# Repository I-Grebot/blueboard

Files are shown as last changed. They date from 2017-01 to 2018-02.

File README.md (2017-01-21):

# BlueBoard v1

The BlueBoard is a small form-factor "all-in-one" electronic board for 2 wheels robots.

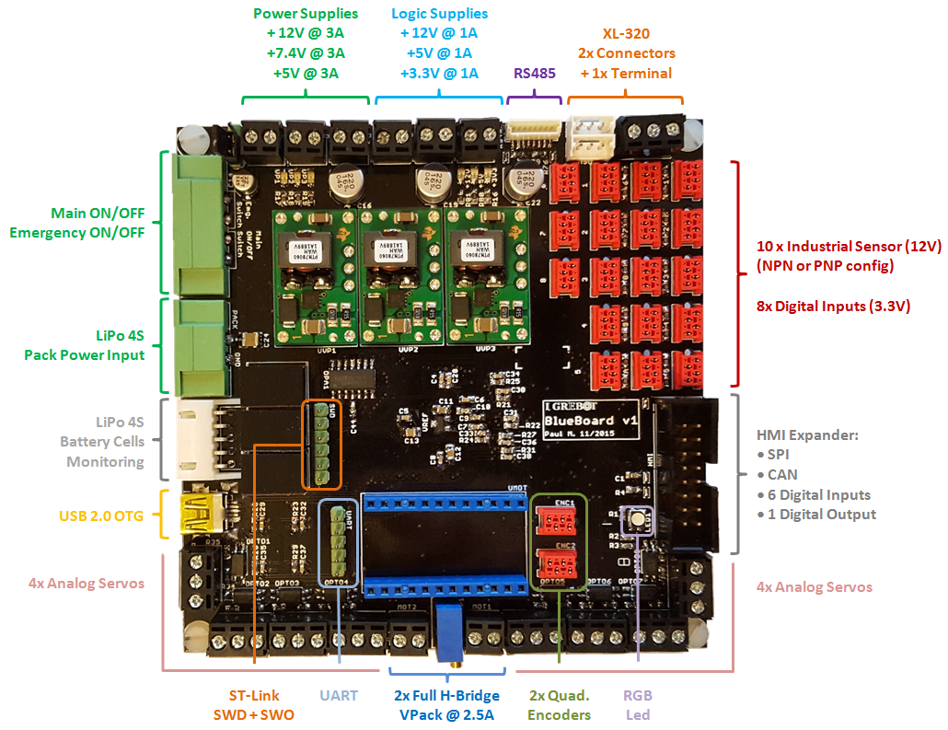
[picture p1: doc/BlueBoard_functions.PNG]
BlueBoard functions


## Features

The board features the following items:

* Compact size: 10 cm x 10 cm
* Single input power-supply (+14V min)
* Integrated Power-Supplies for logic domains using efficient DC/DC step-down regulators:
 * +12V/1A (industrial sensors)
 * +5V/1A (quadrature encoders, other 5V logic)
 * +3/3V/1A (most of digital logic)
* Integrated  Power-Supplies for heavy loads:
 * +12V/3A (generic purpose)
 * +7.4V/3A (dynamixel digital servos ~ can be adjusted)
 * +5V/3A (analog servos)
* Secure and robust Power-pack connector
* Main ON/OFF + Emergency switch connectors
* 2x Full H-Bridge output controls for DRV8842 (2.5A)
* 8x Opto-coupled analog-servos interface (PWM)
* 2x Connectors + 1x terminal for XL-320 digital servos interface
* 2x Quadrature encoders inputs
* 10x Opto-coupled Industrial sensor inputs (NPN/PNP  types selectable)
* 8x Digital Inputs
* RS485 connector for sensor-bus (to be used with ProxTof boards or other)
* UART with RTS/CTS signals
* USB 2.0 OTG connector
* ST-Link with SWD + SWO programming / debugging connector
* Expander connector (to be used with microBoard_HMI):
 * 1x SPI
 * 1x CAN
 * 6x Digital inputs (user selections switches)
 * 1x Digital outputs 

## Troubleshooting

* Mimimum input voltage (TEN / PTN modules) is high for 4S batteries (error due to 6S -> 4S design migration)
* Not working 4S battery cell monitoring analog circuit (to be further checked)

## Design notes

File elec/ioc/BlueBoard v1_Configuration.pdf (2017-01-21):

## BlueBoard Project Configuration Report

# 1. Description

## 1.1. Project

Project Name | BlueBoard
Board Name | BlueBoard
Generated with: | STM32CubeMX 4.12.0
Date | 01/02/2016

## 1.2. MCU

MCU Series | STM32F7
MCU Line | STM32F7x6
MCU name | STM32F746VGTx
MCU Package | LQFP100
MCU Pin number | 100

# 2. Pinout Configuration

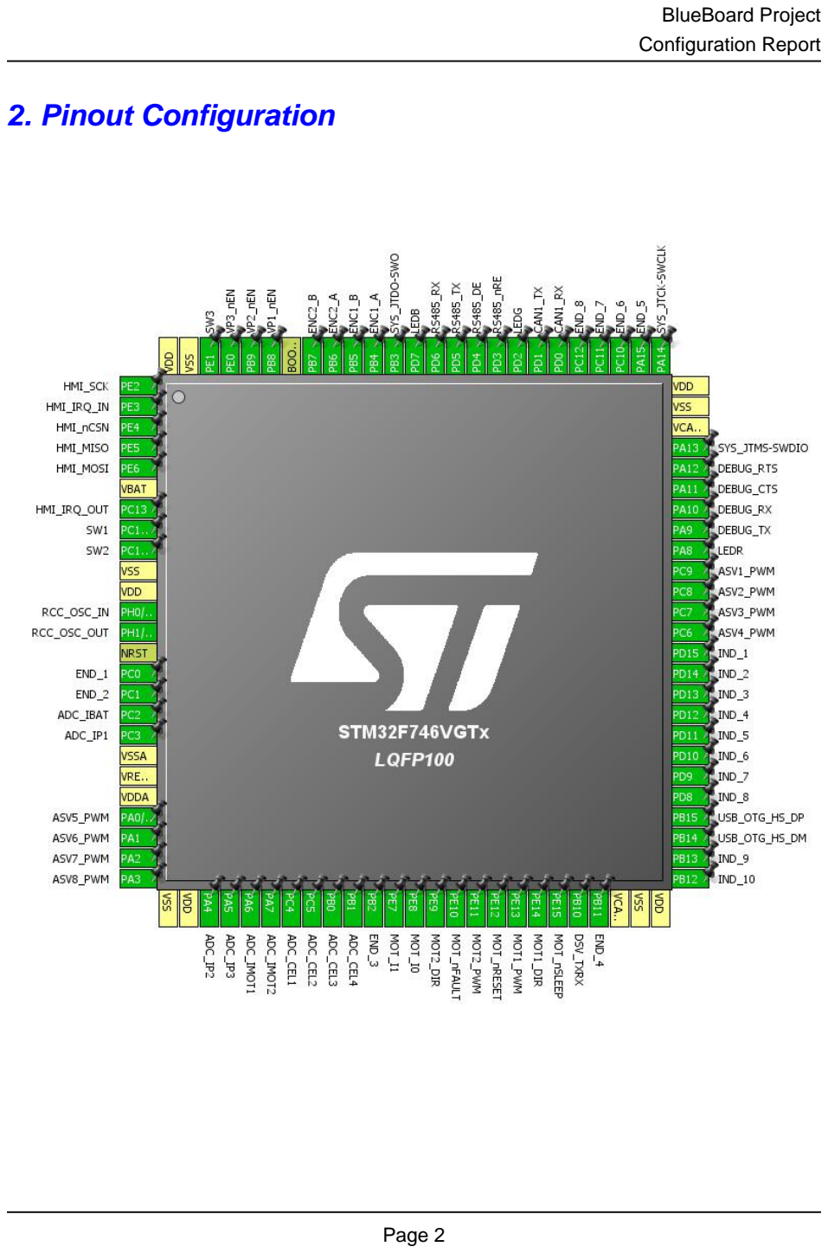
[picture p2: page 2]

# 3. Pins Configuration

Pin Number LQFP100 | Pin Name (function after reset) | Pin Type | Alternate Function(s) | Label
1 | PE2 | I/O | SPI4_SCK | HMI_SCK
2 | PE3 * | I/O | GPIO_Input | HMI_IRQ_IN
3 | PE4 | I/O | SPI4_NSS | HMI_nCSN
4 | PE5 | I/O | SPI4_MISO | HMI_MISO
5 | PE6 | I/O | SPI4_MOSI | HMI_MOSI
6 | VBAT | Power
7 | PC13 * | I/O | GPIO_Output | HMI_IRQ_OUT
8 | PC14/OSC32_IN * | I/O | GPIO_Input | SW1
9 | PC15/OSC32_OUT * | I/O | GPIO_Input | SW2
10 | VSS | Power
11 | VDD | Power
12 | PH0/OSC_IN | I/O | RCC_OSC_IN
13 | PH1/OSC_OUT | I/O | RCC_OSC_OUT
14 | NRST | Reset
15 | PC0 * | I/O | GPIO_Input | END_1
16 | PC1 * | I/O | GPIO_Input | END_2
17 | PC2 | I/O | ADC1_IN12 | ADC_IBAT
18 | PC3 | I/O | ADC1_IN13 | ADC_IP1
19 | VSSA | Power
20 | VREF+ | Power
21 | VDDA | Power
22 | PA0/WKUP | I/O | TIM5_CH1 | ASV5_PWM
23 | PA1 | I/O | TIM5_CH2 | ASV6_PWM
24 | PA2 | I/O | TIM5_CH3 | ASV7_PWM
25 | PA3 | I/O | TIM5_CH4 | ASV8_PWM
26 | VSS | Power
27 | VDD | Power
28 | PA4 | I/O | ADC1_IN4 | ADC_IP2
29 | PA5 | I/O | ADC1_IN5 | ADC_IP3
30 | PA6 | I/O | ADC1_IN6 | ADC_IMOT1
31 | PA7 | I/O | ADC1_IN7 | ADC_IMOT2
32 | PC4 | I/O | ADC1_IN14 | ADC_CEL1
33 | PC5 | I/O | ADC1_IN15 | ADC_CEL2
34 | PB0 | I/O | ADC1_IN8 | ADC_CEL3
35 | PB1 | I/O | ADC1_IN9 | ADC_CEL4
36 | PB2 * | I/O | GPIO_Input | END_3

Pin Number LQFP100 | Pin Name (function after reset) | Pin Type | Alternate Function(s) | Label
37 | PE7 * | I/O | GPIO_Output | MOT_I1
38 | PE8 * | I/O | GPIO_Output | MOT_I0
39 | PE9 | I/O | TIM1_CH1 | MOT2_DIR
40 | PE10 * | I/O | GPIO_Input | MOT_nFAULT
41 | PE11 | I/O | TIM1_CH2 | MOT2_PWM
42 | PE12 * | I/O | GPIO_Output | MOT_nRESET
43 | PE13 | I/O | TIM1_CH3 | MOT1_PWM
44 | PE14 | I/O | TIM1_CH4 | MOT1_DIR
45 | PE15 * | I/O | GPIO_Output | MOT_nSLEEP
46 | PB10 | I/O | USART3_TX | DSV_TXRX
47 | PB11 * | I/O | GPIO_Input | END_4
48 | VCAP_1 | Power
49 | VSS | Power
50 | VDD | Power
51 | PB12 * | I/O | GPIO_Input | IND_10
52 | PB13 * | I/O | GPIO_Input | IND_9
53 | PB14 | I/O | USB_OTG_HS_DM
54 | PB15 | I/O | USB_OTG_HS_DP
55 | PD8 * | I/O | GPIO_Input | IND_8
56 | PD9 * | I/O | GPIO_Input | IND_7
57 | PD10 * | I/O | GPIO_Input | IND_6
58 | PD11 * | I/O | GPIO_Input | IND_5
59 | PD12 * | I/O | GPIO_Input | IND_4
60 | PD13 * | I/O | GPIO_Input | IND_3
61 | PD14 * | I/O | GPIO_Input | IND_2
62 | PD15 * | I/O | GPIO_Input | IND_1
63 | PC6 | I/O | TIM8_CH1 | ASV4_PWM
64 | PC7 | I/O | TIM8_CH2 | ASV3_PWM
65 | PC8 | I/O | TIM8_CH3 | ASV2_PWM
66 | PC9 | I/O | TIM8_CH4 | ASV1_PWM
67 | PA8 * | I/O | GPIO_Output | LEDR
68 | PA9 | I/O | USART1_TX | DEBUG_TX
69 | PA10 | I/O | USART1_RX | DEBUG_RX
70 | PA11 | I/O | USART1_CTS | DEBUG_CTS
71 | PA12 | I/O | USART1_RTS | DEBUG_RTS
72 | PA13 | I/O | SYS_JTMS-SWDIO
73 | VCAP_2 | Power
74 | VSS | Power
75 | VDD | Power

Pin Number LQFP100 | Pin Name (function after reset) | Pin Type | Alternate Function(s) | Label
76 | PA14 | I/O | SYS_JTCK-SWCLK
77 | PA15 * | I/O | GPIO_Input | END_5
78 | PC10 * | I/O | GPIO_Input | END_6
79 | PC11 * | I/O | GPIO_Input | END_7
80 | PC12 * | I/O | GPIO_Input | END_8
81 | PD0 | I/O | CAN1_RX
82 | PD1 | I/O | CAN1_TX
83 | PD2 * | I/O | GPIO_Output | LEDG
84 | PD3 * | I/O | GPIO_Output | RS485_nRE
85 | PD4 * | I/O | GPIO_Output | RS485_DE
86 | PD5 | I/O | USART2_TX | RS485_TX
87 | PD6 | I/O | USART2_RX | RS485_RX
88 | PD7 * | I/O | GPIO_Output | LEDB
89 | PB3 | I/O | SYS_JTDO-SWO
90 | PB4 | I/O | TIM3_CH1 | ENC1_A
91 | PB5 | I/O | TIM3_CH2 | ENC1_B
92 | PB6 | I/O | TIM4_CH1 | ENC2_A
93 | PB7 | I/O | TIM4_CH2 | ENC2_B
94 | BOOT0 | Boot
95 | PB8 * | I/O | GPIO_Output | VP1_nEN
96 | PB9 * | I/O | GPIO_Output | VP2_nEN
97 | PE0 * | I/O | GPIO_Output | VP3_nEN
98 | PE1 * | I/O | GPIO_Input | SW3
99 | VSS | Power
100 | VDD | Power

## * The pin is affected with an I/O function

# 4. Clock Tree Configuration

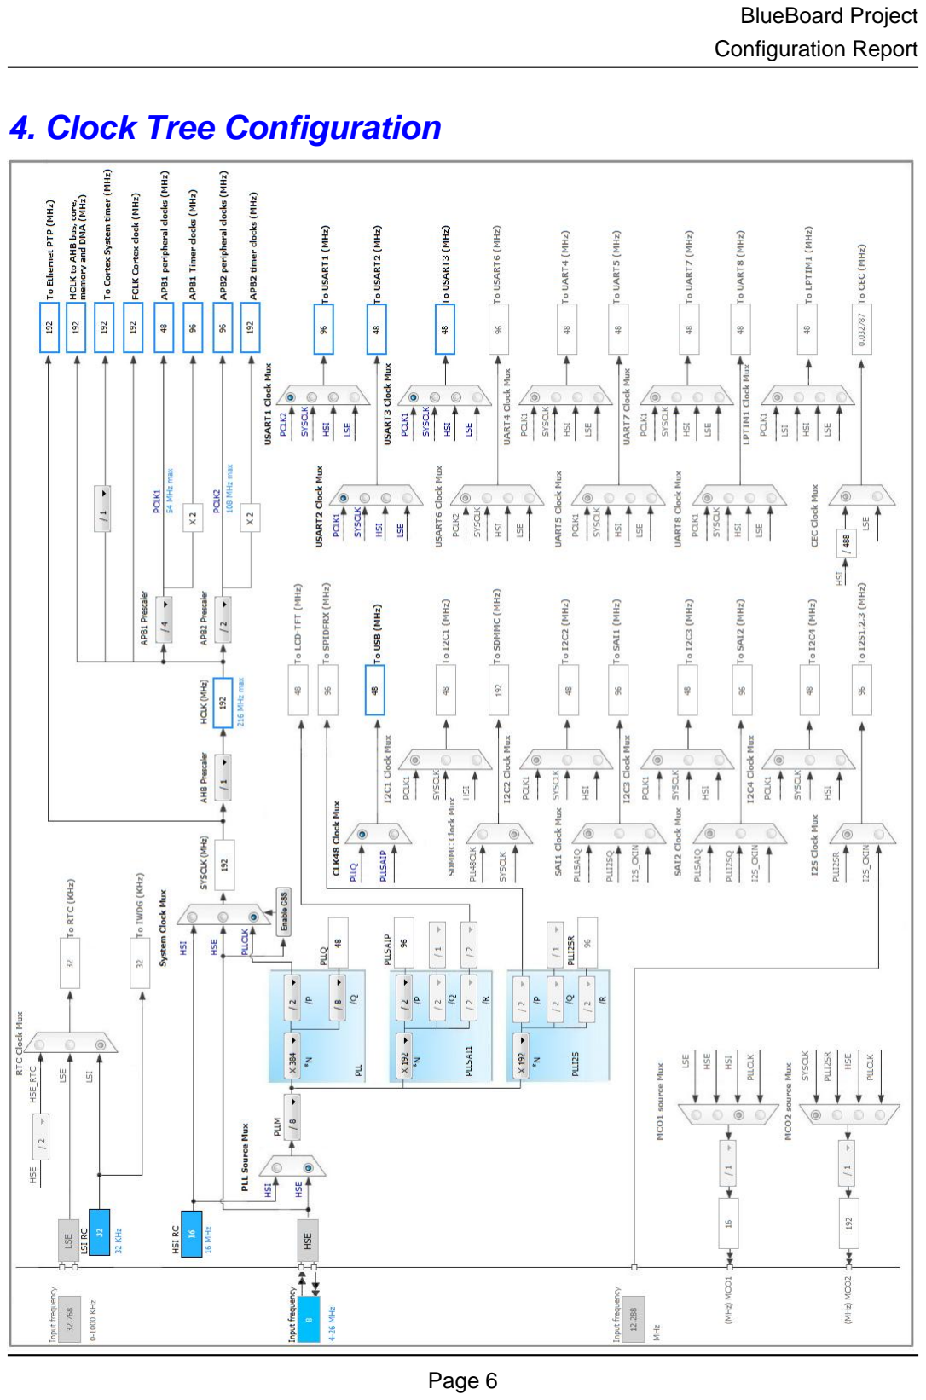
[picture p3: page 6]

# 5. IPs and Middleware Configuration

# 5.1. ADC1

## mode: IN4 mode: IN5 mode: IN6 mode: IN7 mode: IN8 mode: IN9 mode: IN12 mode: IN13 mode: IN14 mode: IN15

## 5.1.1. Parameter Settings:

### ADCs_Common_Settings:

Mode | Independent mode

### ADC_Settings:

Clock Prescaler | PCLK2 divided by 8 *
Resolution | 12 bits (15 ADC Clock cycles)
Data Alignment | Right alignment
Scan Conversion Mode | Disabled
Continuous Conversion Mode | Disabled
Discontinuous Conversion Mode | Disabled
DMA Continuous Requests | Disabled
End Of Conversion Selection | EOC flag at the end of all conversions *

### ADC_Regular_ConversionMode:

Number Of Conversion | 1
External Trigger Conversion Edge | None
Rank | 1
Channel | Channel 4
Sampling Time | 3 Cycles

### ADC_Injected_ConversionMode:

Number Of Conversions | 0

### WatchDog:

Enable Analog WatchDog Mode | false

# 5.2. CAN1

## mode: Mode

## 5.2.1. Parameter Settings:

### Bit Timings Parameters:

Prescaler (for Time Quantum) | 16
Time Quantum | 333.3333333333333 *
Time Quanta in Bit Segment 1 | 6 Times *
Time Quanta in Bit Segment 2 | 5 Times *
Time for one Bit | 4000 *
ReSynchronization Jump Width | 3 Times *

### Basic Parameters:

Time Triggered Communication Mode | Disable
Automatic Bus-Off Management | Disable
Automatic Wake-Up Mode | Disable
No-Automatic Retransmission | Disable
Receive Fifo Locked Mode | Disable
Transmit Fifo Priority | Disable

### Advanced Parameters:

Operating Mode | Normal

# 5.3. RCC

## High Speed Clock (HSE): Crystal/Ceramic Resonator

## 5.3.1. Parameter Settings:

### System Parameters:

VDD voltage (V) | 3.3
Flash Latency(WS) | 6 WS (7 CPU cycle)

### RCC Parameters:

HSI Calibration Value | 16
TIM Prescaler Selection | Disabled

### Power Parameters:

Power Over Drive | Enabled

Power Regulatror Voltage Scale | Power Regulator Voltage Scale 1

# 5.4. SPI4

## Mode: Full-Duplex Master mode: Hardware NSS Signal

## 5.4.1. Parameter Settings:

### Basic Parameters:

Frame Format | Motorola
Data Size | 16 Bits *
First Bit | MSB First

### Clock Parameters:

Prescaler (for Baud Rate) | 256 *
Baud Rate | 375.0 KBits/s *
Clock Polarity (CPOL) | Low
Clock Phase (CPHA) | 1 Edge

### Advanced Parameters:

CRC Calculation | Disabled
NSSP Mode | Enabled
NSS Signal Type | Output Hardware

# 5.5. SYS

## Debug: SWD and Asynchronous Trace

# 5.6. TIM1

## Channel1: PWM Generation CH1 Channel2: PWM Generation CH2 Channel3: PWM Generation CH3 Channel4: PWM Generation CH4

## 5.6.1. Parameter Settings:

### Counter Settings:

Prescaler (PSC - 16 bits value) | 0

Counter Mode | Up
Counter Period (AutoReload Register - 16 bits value ) | 0
Internal Clock Division (CKD) | No Division
Repetition Counter (RCR - 16 bits value) | 0

### Trigger Output (TRGO) Parameters:

Master/Slave Mode | Disable (no sync between this TIM (Master) and its Slaves
Trigger Event Selection TRGO | Reset (UG bit from TIMx_EGR)
Trigger Event Selection TRGO2 | Reset (UG bit from TIMx_EGR)

### Break And Dead Time management - BRK Configuration:

BRK State | Disable
BRK Polarity | High
BRK Filter (4 bits value) | 0

### Break And Dead Time management - BRK2 Configuration:

BRK2 State | Disable
BRK2 Polarity | High
BRK2 Filter (4 bits value) | 0

### Break And Dead Time management - Output Configuration:

Automatic Output State | Disable
Off State Selection for Run Mode (OSSR) | Disable
Off State Selection for Idle Mode (OSSI) | Disable
Lock Configuration | Off

### Clear Input:

Clear Input Source | Disable

### PWM Generation Channel 1:

Mode | PWM mode 1
Pulse (16 bits value) | 0
Fast Mode | Disable
CH Polarity | High
CH Idle State | Reset

### PWM Generation Channel 2:

Mode | PWM mode 1
Pulse (16 bits value) | 0
Fast Mode | Disable
CH Polarity | High
CH Idle State | Reset

### PWM Generation Channel 3:

Mode | PWM mode 1
Pulse (16 bits value) | 0
Fast Mode | Disable
CH Polarity | High
CH Idle State | Reset

### PWM Generation Channel 4:

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

# 5.7. TIM3

## Combined Channels: Encoder Mode

## 5.7.1. Parameter Settings:

### Counter Settings:

Prescaler (PSC - 16 bits value) | 0
Counter Mode | Up
Counter Period (AutoReload Register - 16 bits value ) | 0
Internal Clock Division (CKD) | No Division

### Trigger Output (TRGO) Parameters:

Master/Slave Mode | Disable (no sync between this TIM (Master) and its Slaves
Trigger Event Selection TRGO | Reset (UG bit from TIMx_EGR)

### Encoder:

Encoder Mode | Encoder Mode TI1
____ Parameters for Channel 1 ____
Polarity | Rising Edge
IC Selection | Direct
Prescaler Division Ratio | No division
Input Filter | 0
____ Parameters for Channel 2 ____
Polarity | Rising Edge
IC Selection | Direct
Prescaler Division Ratio | No division
Input Filter | 0

# 5.8. TIM4

## Combined Channels: Encoder Mode

## 5.8.1. Parameter Settings:

### Counter Settings:

Prescaler (PSC - 16 bits value) | 0
Counter Mode | Up
Counter Period (AutoReload Register - 16 bits value ) | 0
Internal Clock Division (CKD) | No Division

### Trigger Output (TRGO) Parameters:

Master/Slave Mode | Disable (no sync between this TIM (Master) and its Slaves
Trigger Event Selection TRGO | Reset (UG bit from TIMx_EGR)

### Encoder:

Encoder Mode | Encoder Mode TI1
____ Parameters for Channel 1 ____
Polarity | Rising Edge
IC Selection | Direct
Prescaler Division Ratio | No division
Input Filter | 0
____ Parameters for Channel 2 ____
Polarity | Rising Edge
IC Selection | Direct
Prescaler Division Ratio | No division
Input Filter | 0

# 5.9. TIM5

## Channel1: PWM Generation CH1 Channel2: PWM Generation CH2 Channel3: PWM Generation CH3 Channel4: PWM Generation CH4

## 5.9.1. Parameter Settings:

### Counter Settings:

Prescaler (PSC - 16 bits value) | 0
Counter Mode | Up
Counter Period (AutoReload Register - 32 bits value ) | 0
Internal Clock Division (CKD) | No Division

### Trigger Output (TRGO) Parameters:

Master/Slave Mode | Disable (no sync between this TIM (Master) and its Slaves

Trigger Event Selection TRGO | Reset (UG bit from TIMx_EGR)

### Clear Input:

Clear Input Source | Disable

### PWM Generation Channel 1:

Mode | PWM mode 1
Pulse (32 bits value) | 0
Fast Mode | Disable
CH Polarity | High

### PWM Generation Channel 2:

Mode | PWM mode 1
Pulse (32 bits value) | 0
Fast Mode | Disable
CH Polarity | High

### PWM Generation Channel 3:

Mode | PWM mode 1
Pulse (32 bits value) | 0
Fast Mode | Disable
CH Polarity | High

### PWM Generation Channel 4:

Mode | PWM mode 1
Pulse (32 bits value) | 0
Fast Mode | Disable
CH Polarity | High

# 5.10. TIM8

## Trigger Source: ITR0 Clock Source : Internal Clock Channel1: PWM Generation CH1 Channel2: PWM Generation CH2 Channel3: PWM Generation CH3 Channel4: PWM Generation CH4

## 5.10.1. Parameter Settings:

### Counter Settings:

Prescaler (PSC - 16 bits value) | 192 *
Counter Mode | Up
Counter Period (AutoReload Register - 16 bits value ) | 9999 *

Internal Clock Division (CKD) | No Division
Repetition Counter (RCR - 16 bits value) | 0
Slave Mode Controller | Slave mode disable

### Trigger Output (TRGO) Parameters:

Master/Slave Mode | Disable (no sync between this TIM (Master) and its Slaves
Trigger Event Selection TRGO | Reset (UG bit from TIMx_EGR)
Trigger Event Selection TRGO2 | Reset (UG bit from TIMx_EGR)

### Break And Dead Time management - BRK Configuration:

BRK State | Disable
BRK Polarity | High
BRK Filter (4 bits value) | 0

### Break And Dead Time management - BRK2 Configuration:

BRK2 State | Disable
BRK2 Polarity | High
BRK2 Filter (4 bits value) | 0

### Break And Dead Time management - Output Configuration:

Automatic Output State | Disable
Off State Selection for Run Mode (OSSR) | Disable
Off State Selection for Idle Mode (OSSI) | Disable
Lock Configuration | Off

### Clear Input:

Clear Input Source | Disable

### PWM Generation Channel 1:

Mode | PWM mode 1
Pulse (16 bits value) | 999 *
Fast Mode | Disable
CH Polarity | High
CH Idle State | Reset

### PWM Generation Channel 2:

Mode | PWM mode 1
Pulse (16 bits value) | 1999 *
Fast Mode | Disable
CH Polarity | High
CH Idle State | Reset

### PWM Generation Channel 3:

Mode | PWM mode 1
Pulse (16 bits value) | 4999 *
Fast Mode | Disable
CH Polarity | High
CH Idle State | Reset

### PWM Generation Channel 4:

Mode | PWM mode 1
Pulse (16 bits value) | 7999 *
Fast Mode | Disable
CH Polarity | High
CH Idle State | Reset

# 5.11. USART1

## Mode: Asynchronous Hardware Flow Control (RS232): CTS/RTS

## 5.11.1. Parameter Settings:

### Basic Parameters:

Baud Rate | 115200
Word Length | 8 Bits (including Parity) *
Parity | None
Stop Bits | 1

### Advanced Parameters:

Data Direction | Receive and Transmit
Over Sampling | 16 Samples
Single Sample | Disable

### Advanced Features:

Auto Baudrate | Disable
TX Pin Active Level Inversion | Disable
RX Pin Active Level Inversion | Disable
Data Inversion | Disable
TX and RX Pins Swapping | Disable
Overrun | Enable
DMA on RX Error | Enable
MSB First | Disable

# 5.12. USART2

## Mode: Asynchronous

## 5.12.1. Parameter Settings:

### Basic Parameters:

Baud Rate | 115200
Word Length | 8 Bits (including Parity) *
Parity | None
Stop Bits | 1

### Advanced Parameters:

Data Direction | Receive and Transmit
Over Sampling | 16 Samples
Single Sample | Disable

### Advanced Features:

Auto Baudrate | Disable
TX Pin Active Level Inversion | Disable
RX Pin Active Level Inversion | Disable
Data Inversion | Disable
TX and RX Pins Swapping | Disable
Overrun | Enable
DMA on RX Error | Enable
MSB First | Disable

# 5.13. USART3

## Mode: Single Wire (Half-Duplex)

## 5.13.1. Parameter Settings:

### Basic Parameters:

Baud Rate | 1000000 *
Word Length | 8 Bits (including Parity) *
Parity | None
Stop Bits | 1

### Advanced Parameters:

Data Direction | Receive and Transmit
Over Sampling | 16 Samples
Single Sample | Disable

### Advanced Features:

Auto Baudrate | Disable
TX Pin Active Level Inversion | Disable
RX Pin Active Level Inversion | Disable

Data Inversion | Disable
TX and RX Pins Swapping | Disable
Overrun | Enable
DMA on RX Error | Enable
MSB First | Disable

# 5.14. USB_OTG_HS

## Internal FS Phy: Device_Only

## 5.14.1. Parameter Settings:

Speed | Device Full Speed 12MBit/s
Endpoint 0 Max Packet size | 64 Bytes
Enable internal IP DMA | Disabled
Physical interface | Internal Phy
Low power | Disabled
Link Power Management | Disabled
Use dedicated end point 1 interrupt | Disabled
VBUS sensing | Disabled

# 5.15. FREERTOS

## mode: Enabled

## 5.15.1. Config parameters:

### Versions:

CMSIS-RTOS version | 1.02
FreeRTOS version | 8.2.1

### Kernel settings:

USE_PREEMPTION | Enabled
CPU_CLOCK_HZ | SystemCoreClock
TICK_RATE_HZ | 1000
MAX_PRIORITIES | 7
MINIMAL_STACK_SIZE | 128
MAX_TASK_NAME_LEN | 16
USE_16_BIT_TICKS | Disabled
IDLE_SHOULD_YIELD | Enabled

USE_MUTEXES | Enabled
USE_RECURSIVE_MUTEXES | Enabled
USE_COUNTING_SEMAPHORES | Enabled
QUEUE_REGISTRY_SIZE | 8
USE_APPLICATION_TASK_TAG | Disabled
TOTAL_HEAP_SIZE | 15360
Memory Management scheme | heap_4
USE_ALTERNATIVE_API | Disabled
ENABLE_BACKWARD_COMPATIBILITY | Enabled
USE_PORT_OPTIMISED_TASK_SELECTION | Disabled
USE_TICKLESS_IDLE | Disabled

### Hook function related definitions:

USE_IDLE_HOOK | Disabled
USE_TICK_HOOK | Disabled
USE_MALLOC_FAILED_HOOK | Disabled
CHECK_FOR_STACK_OVERFLOW | Disabled

### Run time and task stats gathering related definitions:

USE_TRACE_FACILITY | Enabled
GENERATE_RUN_TIME_STATS | Disabled

### Co-routine related definitions:

USE_CO_ROUTINES | Disabled
MAX_CO_ROUTINE_PRIORITIES | 2

### Software timer definitions:

USE_TIMERS | Disabled
TIMER_TASK_PRIORITY | 2
TIMER_QUEUE_LENGTH | 10

### Interrupt nesting behaviour configuration:

LIBRARY_LOWEST_INTERRUPT_PRIORITY | 15
LIBRARY_MAX_SYSCALL_INTERRUPT_PRIORITY | 5

## 5.15.2. Include parameters:

### Include definitions:

vTaskPrioritySet | Enabled
uxTaskPriorityGet | Enabled
vTaskDelete | Enabled
vTaskCleanUpResources | Disabled
vTaskSuspend | Enabled
vTaskDelayUntil | Disabled
vTaskDelay | Enabled
xTaskGetSchedulerState | Enabled

xTaskResumeFromISR | Enabled
xQueueGetMutexHolder | Disabled
xSemaphoreGetMutexHolder | Disabled
pcTaskGetTaskName | Disabled
uxTaskGetStackHighWaterMark | Disabled
xTaskGetCurrentTaskHandle | Disabled
eTaskGetState | Disabled
xEventGroupSetBitFromISR | Disabled
xTimerPendFunctionCall | Disabled

# 5.16. USB_DEVICE

## Class For HS IP: Communication Device Class (Virtual Port Com)

## 5.16.1. Parameter Settings:

### Basic Parameters:

USBD_MAX_NUM_INTERFACES (Maximum number of supported interfaces) | 1
USBD_MAX_NUM_CONFIGURATION (Maximum number of supported configuration) | 1
USBD_MAX_STR_DESC_SIZ (Maximum size for the string descriptors) | 512
USBD_SUPPORT_USER_STRING (Enable user string descriptor) | Disabled
USBD_SELF_POWERED (Enabled self power) | Enabled
USBD_DEBUG_LEVEL (USBD Debug Level) | 0: No debug message
USBD_LPM_ENABLED (Link Power Management) | 1: Link Power Management supported

### Class Parameters:

USBD_CDC_INTERVAL (Number of micro-frames interval) | 1000

## 5.16.2. Device Descriptor:

### Device Descriptor:

VID (Vendor IDentifier) | 1155
LANGID_STRING (Language Identifier) | English(United States)
MANUFACTURER_STRING (Manufacturer Identifier) | IGreBot *

### Device Descriptor HS:

PID (Product IDentifier) | 22336
PRODUCT_STRING (Product Identifier) | BlueBoard *
SERIALNUMBER_STRING (Serial number) | 00000000001A
CONFIGURATION_STRING (Configuration Identifier) | CDC Config
INTERFACE_STRING (Interface Identifier) | CDC Interface

### * User modified value

# 6. System Configuration

# 6.1. GPIO configuration

IP | Pin | Signal | GPIO mode | GPIO pull/up pull down | Max Speed | User Label
ADC1 | PC2 | ADC1_IN12 | Analog mode | No pull-up and no pull-down | n/a | ADC_IBAT
| PC3 | ADC1_IN13 | Analog mode | No pull-up and no pull-down | n/a | ADC_IP1
| PA4 | ADC1_IN4 | Analog mode | No pull-up and no pull-down | n/a | ADC_IP2
| PA5 | ADC1_IN5 | Analog mode | No pull-up and no pull-down | n/a | ADC_IP3
| PA6 | ADC1_IN6 | Analog mode | No pull-up and no pull-down | n/a | ADC_IMOT1
| PA7 | ADC1_IN7 | Analog mode | No pull-up and no pull-down | n/a | ADC_IMOT2
| PC4 | ADC1_IN14 | Analog mode | No pull-up and no pull-down | n/a | ADC_CEL1
| PC5 | ADC1_IN15 | Analog mode | No pull-up and no pull-down | n/a | ADC_CEL2
| PB0 | ADC1_IN8 | Analog mode | No pull-up and no pull-down | n/a | ADC_CEL3
| PB1 | ADC1_IN9 | Analog mode | No pull-up and no pull-down | n/a | ADC_CEL4
CAN1 | PD0 | CAN1_RX | Alternate Function Push Pull | No pull-up and no pull-down | High *
| PD1 | CAN1_TX | Alternate Function Push Pull | No pull-up and no pull-down | High *
RCC | PH0/OSC_I N | RCC_OSC_IN | n/a | n/a | n/a
| PH1/OSC_O UT | RCC_OSC_OUT | n/a | n/a | n/a
SPI4 | PE2 | SPI4_SCK | Alternate Function Push Pull | No pull-up and no pull-down | High * | HMI_SCK
| PE4 | SPI4_NSS | Alternate Function Push Pull | No pull-up and no pull-down | High * | HMI_nCSN
| PE5 | SPI4_MISO | Alternate Function Push Pull | No pull-up and no pull-down | High * | HMI_MISO
| PE6 | SPI4_MOSI | Alternate Function Push Pull | No pull-up and no pull-down | High * | HMI_MOSI
SYS | PA13 | SYS_JTMS-SWDIO | n/a | n/a | n/a
| PA14 | SYS_JTCK-SWCLK | n/a | n/a | n/a
| PB3 | SYS_JTDO-SWO | n/a | n/a | n/a
TIM1 | PE9 | TIM1_CH1 | Alternate Function Push Pull | No pull-up and no pull-down | Low | MOT2_DIR
| PE11 | TIM1_CH2 | Alternate Function Push Pull | No pull-up and no pull-down | Low | MOT2_PWM
| PE13 | TIM1_CH3 | Alternate Function Push Pull | No pull-up and no pull-down | Low | MOT1_PWM
| PE14 | TIM1_CH4 | Alternate Function Push Pull | No pull-up and no pull-down | Low | MOT1_DIR
TIM3 | PB4 | TIM3_CH1 | Alternate Function Push Pull | No pull-up and no pull-down | Low | ENC1_A
| PB5 | TIM3_CH2 | Alternate Function Push Pull | No pull-up and no pull-down | Low | ENC1_B
TIM4 | PB6 | TIM4_CH1 | Alternate Function Push Pull | No pull-up and no pull-down | Low | ENC2_A
| PB7 | TIM4_CH2 | Alternate Function Push Pull | No pull-up and no pull-down | Low | ENC2_B

IP | Pin | Signal | GPIO mode | GPIO pull/up pull down

## Max Speed

## User Label

TIM5 | PA0/WKUP | TIM5_CH1 | Alternate Function Push Pull | No pull-up and no pull-down | Low | ASV5_PWM
| PA1 | TIM5_CH2 | Alternate Function Push Pull | No pull-up and no pull-down | Low | ASV6_PWM
| PA2 | TIM5_CH3 | Alternate Function Push Pull | No pull-up and no pull-down | Low | ASV7_PWM
| PA3 | TIM5_CH4 | Alternate Function Push Pull | No pull-up and no pull-down | Low | ASV8_PWM
TIM8 | PC6 | TIM8_CH1 | Alternate Function Push Pull | No pull-up and no pull-down | Low | ASV4_PWM
| PC7 | TIM8_CH2 | Alternate Function Push Pull | No pull-up and no pull-down | Low | ASV3_PWM
| PC8 | TIM8_CH3 | Alternate Function Push Pull | No pull-up and no pull-down | Low | ASV2_PWM
| PC9 | TIM8_CH4 | Alternate Function Push Pull | No pull-up and no pull-down | Low | ASV1_PWM
USART1 | PA9 | USART1_TX | Alternate Function Push Pull | Pull-up | High * | DEBUG_TX
| PA10 | USART1_RX | Alternate Function Push Pull | Pull-up | High * | DEBUG_RX
PA11 | USART1_CTS Alternate Function Push Pull | No pull-up and no pull-down | High * | DEBUG_CTS
PA12 | USART1_RTS Alternate Function Push Pull | No pull-up and no pull-down | High * | DEBUG_RTS
USART2 | PD5 | USART2_TX | Alternate Function Push Pull | Pull-up | High * | RS485_TX
| PD6 | USART2_RX | Alternate Function Push Pull | Pull-up | High * | RS485_RX
USART3 | PB10 | USART3_TX | Alternate Function Open Drain | Pull-up | High * | DSV_TXRX
USB_OTG_ HS | PB14 | USB_OTG_HS_ DM | Alternate Function Push Pull | No pull-up and no pull-down | High *
| PB15 | USB_OTG_HS_ DP | Alternate Function Push Pull | No pull-up and no pull-down | High *
GPIO | PE3 | GPIO_Input | Input mode | No pull-up and no pull-down | n/a | HMI_IRQ_IN
| PC13 | GPIO_Output | Output Push Pull | No pull-up and no pull-down | Low | HMI_IRQ_OUT
| PC14/OSC3 2_IN | GPIO_Input | Input mode | No pull-up and no pull-down | n/a | SW1
| PC15/OSC3 2_OUT | GPIO_Input | Input mode | No pull-up and no pull-down | n/a | SW2
| PC0 | GPIO_Input | Input mode | No pull-up and no pull-down | n/a | END_1
| PC1 | GPIO_Input | Input mode | No pull-up and no pull-down | n/a | END_2
| PB2 | GPIO_Input | Input mode | No pull-up and no pull-down | n/a | END_3
| PE7 | GPIO_Output | Output Push Pull | No pull-up and no pull-down | Low | MOT_I1
| PE8 | GPIO_Output | Output Push Pull | No pull-up and no pull-down | Low | MOT_I0
| PE10 | GPIO_Input | Input mode | No pull-up and no pull-down | n/a | MOT_nFAULT
| PE12 | GPIO_Output | Output Push Pull | No pull-up and no pull-down | Low | MOT_nRESET
| PE15 | GPIO_Output | Output Push Pull | No pull-up and no pull-down | Low | MOT_nSLEEP
| PB11 | GPIO_Input | Input mode | No pull-up and no pull-down | n/a | END_4
| PB12 | GPIO_Input | Input mode | No pull-up and no pull-down | n/a | IND_10
| PB13 | GPIO_Input | Input mode | No pull-up and no pull-down | n/a | IND_9
| PD8 | GPIO_Input | Input mode | No pull-up and no pull-down | n/a | IND_8
| PD9 | GPIO_Input | Input mode | No pull-up and no pull-down | n/a | IND_7
| PD10 | GPIO_Input | Input mode | No pull-up and no pull-down | n/a | IND_6

IP | Pin | Signal | GPIO mode | GPIO pull/up pull down | Max Speed | User Label
| PD11 | GPIO_Input | Input mode | No pull-up and no pull-down | n/a | IND_5
| PD12 | GPIO_Input | Input mode | No pull-up and no pull-down | n/a | IND_4
| PD13 | GPIO_Input | Input mode | No pull-up and no pull-down | n/a | IND_3
| PD14 | GPIO_Input | Input mode | No pull-up and no pull-down | n/a | IND_2
| PD15 | GPIO_Input | Input mode | No pull-up and no pull-down | n/a | IND_1
| PA8 | GPIO_Output | Output Push Pull | No pull-up and no pull-down | Low | LEDR
| PA15 | GPIO_Input | Input mode | No pull-up and no pull-down | n/a | END_5
| PC10 | GPIO_Input | Input mode | No pull-up and no pull-down | n/a | END_6
| PC11 | GPIO_Input | Input mode | No pull-up and no pull-down | n/a | END_7
| PC12 | GPIO_Input | Input mode | No pull-up and no pull-down | n/a | END_8
| PD2 | GPIO_Output | Output Push Pull | No pull-up and no pull-down | Low | LEDG
| PD3 | GPIO_Output | Output Push Pull | No pull-up and no pull-down | Low | RS485_nRE
| PD4 | GPIO_Output | Output Push Pull | No pull-up and no pull-down | Low | RS485_DE
| PD7 | GPIO_Output | Output Push Pull | No pull-up and no pull-down | Low | LEDB
| PB8 | GPIO_Output | Output Push Pull | No pull-up and no pull-down | Low | VP1_nEN
| PB9 | GPIO_Output | Output Push Pull | No pull-up and no pull-down | Low | VP2_nEN
| PE0 | GPIO_Output | Output Push Pull | No pull-up and no pull-down | Low | VP3_nEN
| PE1 | GPIO_Input | Input mode | No pull-up and no pull-down | n/a | SW3

# 6.2. DMA configuration

## nothing configured in DMA service

# 6.3. NVIC configuration

Interrupt Table | Enable | Preenmption Priority | SubPriority
Non maskable interrupt | true | 0 | 0
System tick timer | true | 15 | 0
USB On The Go HS global interrupt | true | 5 | 0
Hard fault interrupt | unused
Memory management fault | unused
Pre-fetch fault, memory access fault | unused
Undefined instruction or illegal state | unused
Debug monitor | unused
PVD interrupt through EXTI line 16 | unused
Flash global interrupt | unused
RCC global interrupt | unused
ADC1, ADC2 and ADC3 global interrupts | unused
CAN1 TX interrupts | unused
CAN1 RX0 interrupts | unused
CAN1 RX1 interrupt | unused
CAN1 SCE interrupt | unused
TIM1 break interrupt and TIM9 global interrupt | unused
TIM1 update interrupt and TIM10 global interrupt | unused
TIM1 trigger and commutation interrupts and TIM11 global interrupt | unused
TIM1 capture compare interrupt | unused
TIM3 global interrupt | unused
TIM4 global interrupt | unused
USART1 global interrupt | unused
USART2 global interrupt | unused
USART3 global interrupt | unused
TIM8 break interrupt and TIM12 global interrupt | unused
TIM8 update interrupt and TIM13 global interrupt | unused
TIM8 trigger and commutation interrupts and TIM14 global interrupt | unused
TIM8 capture compare interrupt | unused
TIM5 global interrupt | unused
USB On The Go HS End Point 1 Out global interrupt | unused
USB On The Go HS End Point 1 In global interrupt | unused
SPI4 global interrupt | unused

### * User modified value

# 7. Power Plugin report

## 7.1. Microcontroller Selection

Series | STM32F7
Line | STM32F7x6
MCU | STM32F746VGTx
Datasheet | 027590_Rev1

## 7.2. Parameter Selection

Temperature | 25
Vdd | 3.3

# 8. Software Project

## 8.1. Project Settings

Name | Value
Project Name | BlueBoard
Project Folder | C:\Users\Paul\Documents\Work\Igrebot\SVN\trunk\Elec\2016\BlueBoard v1\ioc
Toolchain / IDE | TrueSTUDIO
Firmware Package Name and Version | STM32Cube FW_F7 V1.3.1

## 8.2. Code Generation Settings

Name | Value
STM32Cube Firmware Library Package | Copy all used libraries into the project folder
Generate peripheral initialization as a pair of '.c/.h' files | No
Backup previously generated files when re-generating | No
Delete previously generated files when not re-generated | Yes
Set all free pins as analog (to optimize the power consumption) | No

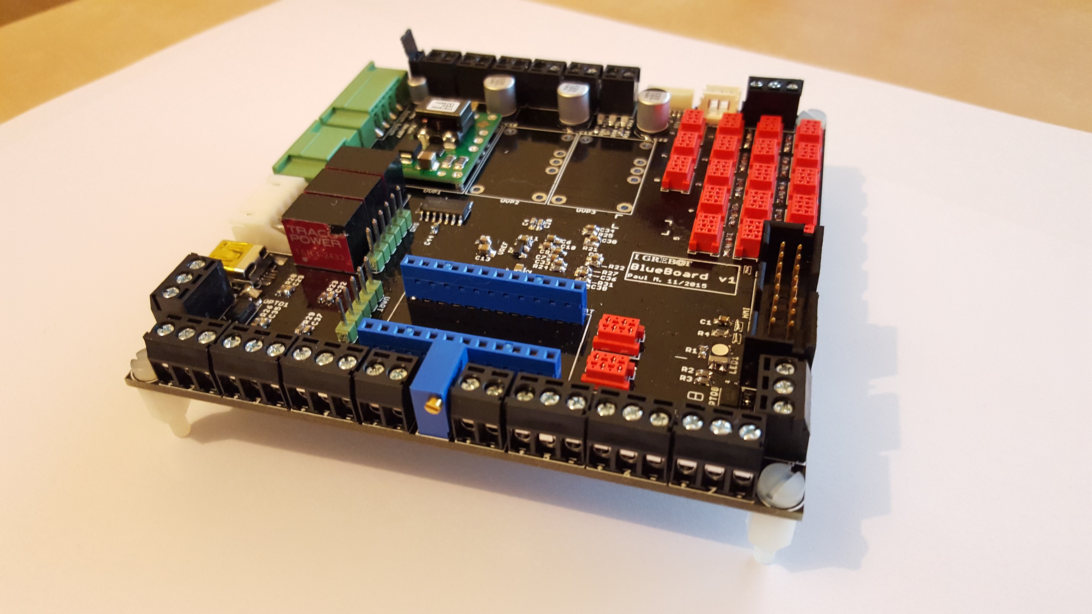
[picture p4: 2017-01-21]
doc/photos/selec2/side2.jpg

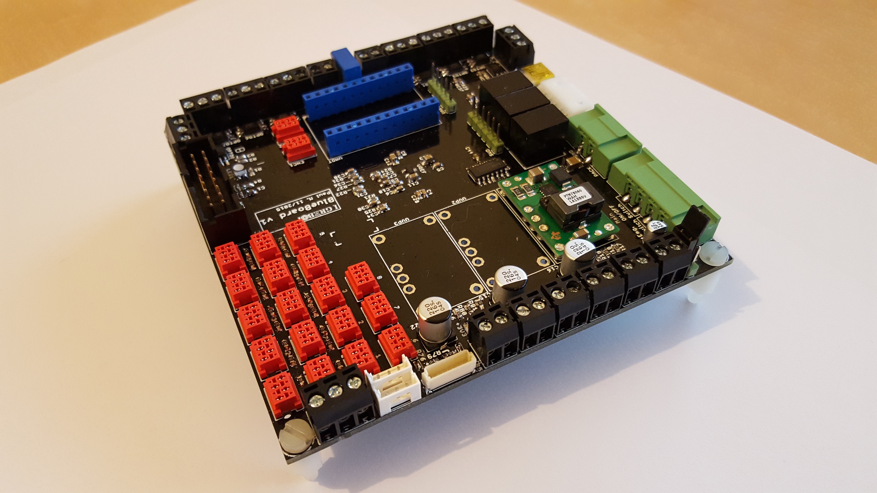
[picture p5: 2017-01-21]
doc/photos/selec2/side1.jpg

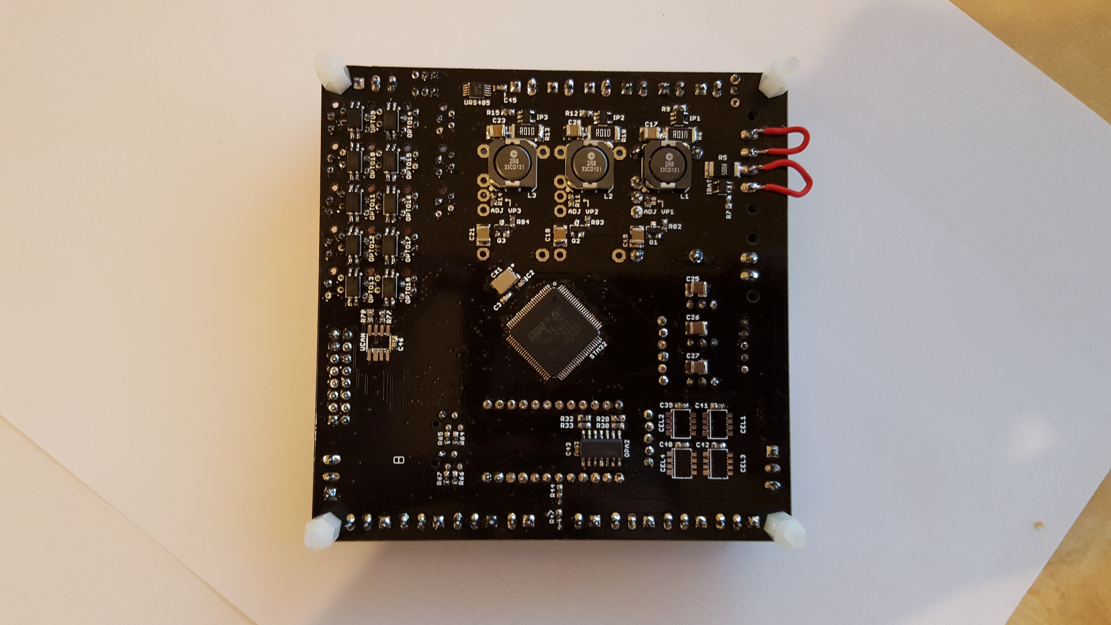
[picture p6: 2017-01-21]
doc/photos/selec2/bot.jpg

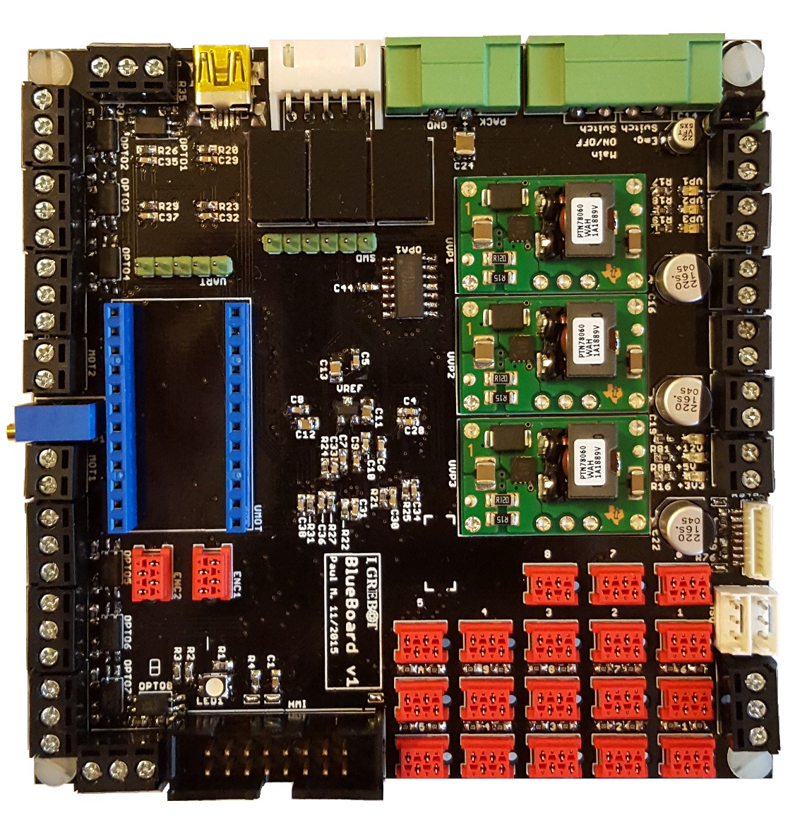
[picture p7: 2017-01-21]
doc/photos/selec2/top_cleaned.jpg

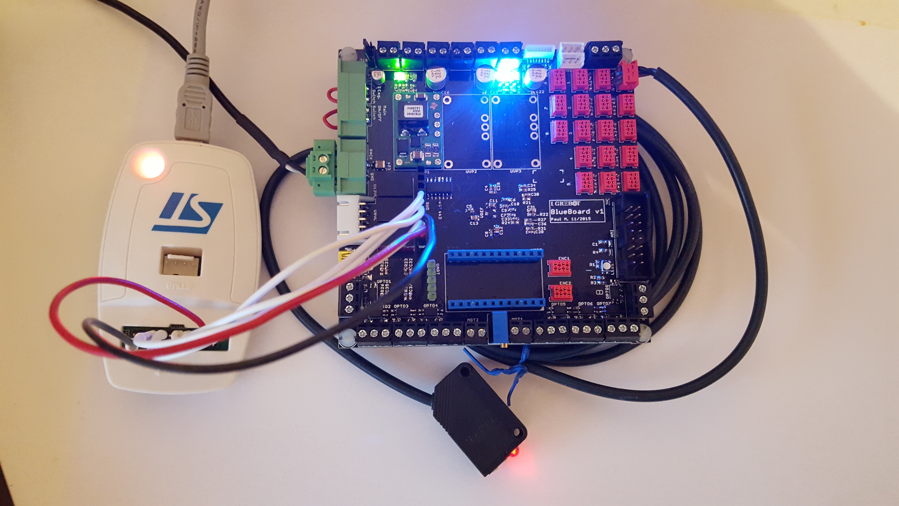
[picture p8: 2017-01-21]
doc/photos/selec2/powered-up.jpg

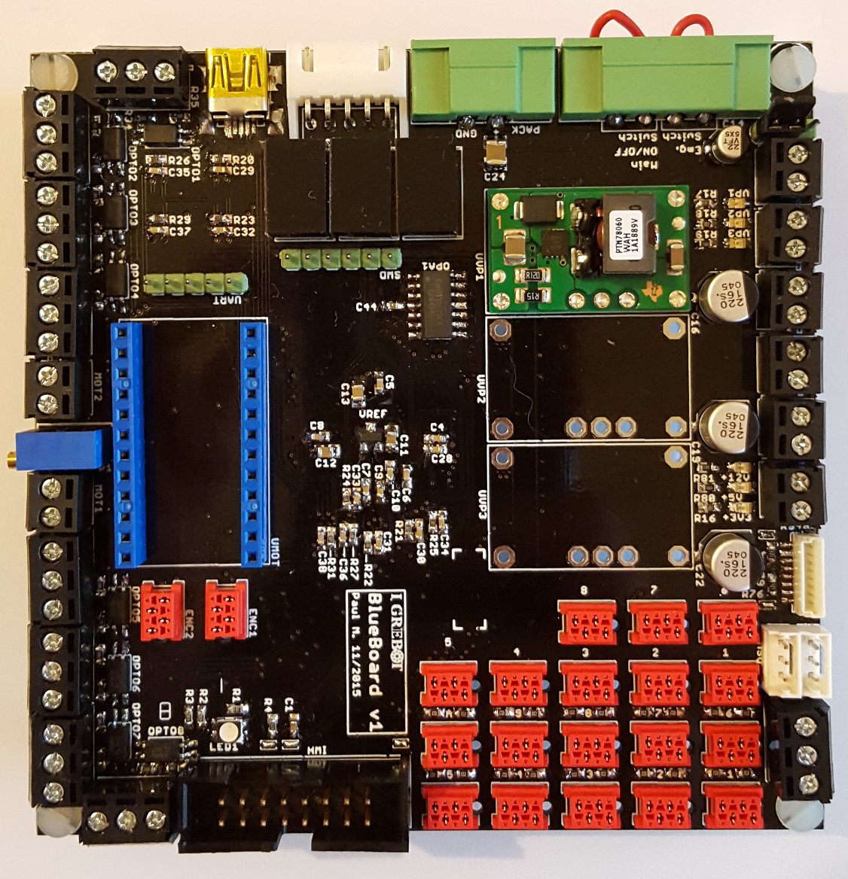
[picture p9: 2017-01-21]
doc/photos/selec2/top.jpg

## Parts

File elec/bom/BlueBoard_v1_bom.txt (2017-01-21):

Partlist exported from C:/Users/Paul/Documents/Work/Igrebot/SVN/trunk/Elec/2016/BlueBoard v1/src/BlueBoard_v1.sch at 01/11/2015 20:36:05

Assembly variant: 

Part         Value                  Device                 Package                Description                                       
ASV1         CON_3.5_3              CON_3.5_3              CON_3.5_3                                                                
ASV2         CON_3.5_3              CON_3.5_3              CON_3.5_3                                                                
ASV3         CON_3.5_3              CON_3.5_3              CON_3.5_3                                                                
ASV4         CON_3.5_3              CON_3.5_3              CON_3.5_3                                                                
ASV5         CON_3.5_3              CON_3.5_3              CON_3.5_3                                                                
ASV6         CON_3.5_3              CON_3.5_3              CON_3.5_3                                                                
ASV7         CON_3.5_3              CON_3.5_3              CON_3.5_3                                                                
ASV8         CON_3.5_3              CON_3.5_3              CON_3.5_3                                                                
BAT1         MC15-GF-3.81-LR_2      MC15-GF-3.81-LR_2      CON_3.81_LR_2                                                            
BAT2         JST-XH-S_5             JST-XH-S_5             JST-XH-5S                                                                
C1           100nF                  C-EUC0603              C0603                  CAPACITOR, European symbol                        
C2           18 pF                  C-EUC0603              C0603                  CAPACITOR, European symbol                        
C3           18 pF                  C-EUC0603              C0603                  CAPACITOR, European symbol                        
C4           100nF                  C-EUC0603              C0603                  CAPACITOR, European symbol                        
C5           100nF                  C-EUC0603              C0603                  CAPACITOR, European symbol                        
C6           100nF                  C-EUC0603              C0603                  CAPACITOR, European symbol                        
C7           100nF                  C-EUC0603              C0603                  CAPACITOR, European symbol                        
C8           100nF                  C-EUC0603              C0603                  CAPACITOR, European symbol                        
C9           10nF                   C-EUC0603              C0603                  CAPACITOR, European symbol                        
C10          10nF                   C-EUC0603              C0603                  CAPACITOR, European symbol                        
C11          1uF                    C-EUC0805              C0805                  CAPACITOR, European symbol                        
C12          2.2uF                  C-EUC0805              C0805                  CAPACITOR, European symbol                        
C13          2.2uF                  C-EUC0805              C0805                  CAPACITOR, European symbol                        
C14          470uF                  CPOL-EUB               PANASONIC_B            POLARIZED CAPACITOR, European symbol              
C15          22uF                   C-EUC3225              C3225                  CAPACITOR, European symbol                        
C16          470uF                  CPOL-EUD               PANASONIC_D            POLARIZED CAPACITOR, European symbol              
C17          1uF                    C-EUC3225              C3225                  CAPACITOR, European symbol                        
C18          22uF                   C-EUC3225              C3225                  CAPACITOR, European symbol                        
C19          470uF                  CPOL-EUD               PANASONIC_D            POLARIZED CAPACITOR, European symbol              
C20          1uF                    C-EUC3225              C3225                  CAPACITOR, European symbol                        
C21          22uF                   C-EUC3225              C3225                  CAPACITOR, European symbol                        
C22          470uF                  CPOL-EUD               PANASONIC_D            POLARIZED CAPACITOR, European symbol              
C23          1uF                    C-EUC3225              C3225                  CAPACITOR, European symbol                        
C24          22uF                   C-EUC3225              C3225                  CAPACITOR, European symbol                        
C25          47uF                   C-EUC1210              C1210                  CAPACITOR, European symbol                        
C26          47uF                   C-EUC1210              C1210                  CAPACITOR, European symbol                        
C27          47uF                   C-EUC1210              C1210                  CAPACITOR, European symbol                        
C28          100nF                  C-EUC0603              C0603                  CAPACITOR, European symbol                        
C29          100nF                  C-EUC0603              C0603                  CAPACITOR, European symbol                        
C30          3.3nF                  C-EUC0603              C0603                  CAPACITOR, European symbol                        
C31          3.3nF                  C-EUC0603              C0603                  CAPACITOR, European symbol                        
C32          100nF                  C-EUC0603              C0603                  CAPACITOR, European symbol                        
C33          3.3nF                  C-EUC0603              C0603                  CAPACITOR, European symbol                        
C34          3.3nF                  C-EUC0603              C0603                  CAPACITOR, European symbol                        
C35          100nF                  C-EUC0603              C0603                  CAPACITOR, European symbol                        
C36          3.3nF                  C-EUC0603              C0603                  CAPACITOR, European symbol                        
C37          100nF                  C-EUC0603              C0603                  CAPACITOR, European symbol                        
C38          3.3nF                  C-EUC0603              C0603                  CAPACITOR, European symbol                        
C39          220nF                  C-EUC0603              C0603                  CAPACITOR, European symbol                        
C40          220nF                  C-EUC0603              C0603                  CAPACITOR, European symbol                        
C41          220nF                  C-EUC0603              C0603                  CAPACITOR, European symbol                        
C42          220nF                  C-EUC0603              C0603                  CAPACITOR, European symbol                        
C43          100nF                  C-EUC0603              C0603                  CAPACITOR, European symbol                        
C44          100nF                  C-EUC0603              C0603                  CAPACITOR, European symbol                        
C45          100 nF                 C-EUC0603K             C0603K                 CAPACITOR, European symbol                        
C46          100nF                  C-EUC0603              C0603                  CAPACITOR, European symbol                        
CEL1         LT1990                 LT1990                 S8                                                                       
CEL2         LT1990                 LT1990                 S8                                                                       
CEL3         LT1990                 LT1990                 S8                                                                       
CEL4         LT1990                 LT1990                 S8                                                                       
CX1          XTAL_5X3               XTAL_5X3               CRYSTAL-OSC-SMD-5X3                                                      
DSV1         CON_2.00_MOLEX-53253_3 CON_2.00_MOLEX-53253_3 CON_2.00_MOLEX-53253_3                                                   
DSV2         CON_2.00_MOLEX-53253_3 CON_2.00_MOLEX-53253_3 CON_2.00_MOLEX-53253_3                                                   
DSV3         CON_3.5_3              CON_3.5_3              CON_3.5_3                                                                
ENC1         CON_1.27_4             CON_1.27_4             CON_1.27_4                                                               
ENC2         CON_1.27_4             CON_1.27_4             CON_1.27_4                                                               
END1         CON_1.27_4             CON_1.27_4             CON_1.27_4                                                               
END2         CON_1.27_4             CON_1.27_4             CON_1.27_4                                                               
END3         CON_1.27_4             CON_1.27_4             CON_1.27_4                                                               
END4         CON_1.27_4             CON_1.27_4             CON_1.27_4                                                               
END5         CON_1.27_4             CON_1.27_4             CON_1.27_4                                                               
END6         CON_1.27_4             CON_1.27_4             CON_1.27_4                                                               
END7         CON_1.27_4             CON_1.27_4             CON_1.27_4                                                               
END8         CON_1.27_4             CON_1.27_4             CON_1.27_4                                                               
HMI          HE10_V_16              HE10_V_16              CON_2X_2.54_V_16                                                         
IBAT         INA138                 INA138                 DBV_05                                                                   
IND1         CON_1.27_4             CON_1.27_4             CON_1.27_4                                                               
IND2         CON_1.27_4             CON_1.27_4             CON_1.27_4                                                               
IND3         CON_1.27_4             CON_1.27_4             CON_1.27_4                                                               
IND4         CON_1.27_4             CON_1.27_4             CON_1.27_4                                                               
IND5         CON_1.27_4             CON_1.27_4             CON_1.27_4                                                               
IND6         CON_1.27_4             CON_1.27_4             CON_1.27_4                                                               
IND7         CON_1.27_4             CON_1.27_4             CON_1.27_4                                                               
IND8         CON_1.27_4             CON_1.27_4             CON_1.27_4                                                               
IND9         CON_1.27_4             CON_1.27_4             CON_1.27_4                                                               
IND10        CON_1.27_4             CON_1.27_4             CON_1.27_4                                                               
IP1          INA138                 INA138                 DBV_05                                                                   
IP2          INA138                 INA138                 DBV_05                                                                   
IP3          INA138                 INA138                 DBV_05                                                                   
L1           2.2 uH                 DR1030                 DR1030                 DR1030 Series Low Profile Power Inductors         
L2           2.2 uH                 DR1030                 DR1030                 DR1030 Series Low Profile Power Inductors         
L3           2.2 uH                 DR1030                 DR1030                 DR1030 Series Low Profile Power Inductors         
LED1                                LEDCHIP-LED0805        CHIP-LED0805           LED                                               
LED2                                LEDCHIP-LED0805        CHIP-LED0805           LED                                               
LED3                                LEDCHIP-LED0805        CHIP-LED0805           LED                                               
LED4                                LEDCHIP-LED0805        CHIP-LED0805           LED                                               
LED5                                LEDCHIP-LED0805        CHIP-LED0805           LED                                               
LED6                                LEDCHIP-LED0805        CHIP-LED0805           LED                                               
LED7                                LEDCHIP-LED0805        CHIP-LED0805           LED                                               
LOGO_IGREBOT LOGO_IGREBOT12X2MM     LOGO_IGREBOT12X2MM     IGREBOT_12X2MM                                                           
LOGO_LAYERS  LAYERS_CHECK4_LAYERS   LAYERS_CHECK4_LAYERS   LAYERS_CHECK_4                                                           
MOT1         CON_3.5_2              CON_3.5_2              CON_3.5_2                                                                
MOT2         CON_3.5_2              CON_3.5_2              CON_3.5_2                                                                
OPA1         OPA4340U               OPA4340U               SO14                   Operational Amplifiers                            
OPA2         OPA4340U               OPA4340U               SO14                   Operational Amplifiers                            
OPTO1        EL3H7-G                EL3H7-G                SSOP_4                                                                   
OPTO2        EL3H7-G                EL3H7-G                SSOP_4                                                                   
OPTO3        EL3H7-G                EL3H7-G                SSOP_4                                                                   
OPTO4        EL3H7-G                EL3H7-G                SSOP_4                                                                   
OPTO5        EL3H7-G                EL3H7-G                SSOP_4                                                                   
OPTO6        EL3H7-G                EL3H7-G                SSOP_4                                                                   
OPTO7        EL3H7-G                EL3H7-G                SSOP_4                                                                   
OPTO8        EL3H7-G                EL3H7-G                SSOP_4                                                                   
OPTO9        EL3H4-G                EL3H4-G                SSOP_4                                                                   
OPTO10       EL3H4-G                EL3H4-G                SSOP_4                                                                   
OPTO11       EL3H4-G                EL3H4-G                SSOP_4                                                                   
OPTO12       EL3H4-G                EL3H4-G                SSOP_4                                                                   
OPTO13       EL3H4-G                EL3H4-G                SSOP_4                                                                   
OPTO14       EL3H4-G                EL3H4-G                SSOP_4                                                                   
OPTO15       EL3H4-G                EL3H4-G                SSOP_4                                                                   
OPTO16       EL3H4-G                EL3H4-G                SSOP_4                                                                   
OPTO17       EL3H4-G                EL3H4-G                SSOP_4                                                                   
OPTO18       EL3H4-G                EL3H4-G                SSOP_4                                                                   
P1           47k                    R-TRIMMT93XB           RTRIMT93XB             Trimm resistor                                    
Q1           BSS138                 MOSFET-NCHANNELBSS138  SOT23                  Common NMOSFET Parts                              
Q2           BSS138                 MOSFET-NCHANNELBSS138  SOT23                  Common NMOSFET Parts                              
Q3           BSS138                 MOSFET-NCHANNELBSS138  SOT23                  Common NMOSFET Parts                              
R1           270                    R-EU_R0603             R0603                  RESISTOR, European symbol                         
R2           270                    R-EU_R0603             R0603                  RESISTOR, European symbol                         
R3           270                    R-EU_R0603             R0603                  RESISTOR, European symbol                         
R4           50k                    R-EU_R0603             R0603                  RESISTOR, European symbol                         
R5           R005                   R-EU_R2512             R2512                  RESISTOR, European symbol                         
R6           R01                    R-EU_R2512             R2512                  RESISTOR, European symbol                         
R7           300k                   R-EU_R0603             R0603                  RESISTOR, European symbol                         
R8           21k                    R-EU_R0603             R0603                  RESISTOR, European symbol                         
R9           500k                   R-EU_R0603             R0603                  RESISTOR, European symbol                         
R10          R01                    R-EU_R2512             R2512                  RESISTOR, European symbol                         
R11          7.5k                   R-EU_R0603             R0603                  RESISTOR, European symbol                         
R12          500k                   R-EU_R0603             R0603                  RESISTOR, European symbol                         
R13          R01                    R-EU_R2512             R2512                  RESISTOR, European symbol                         
R14          383k                   R-EU_R0603             R0603                  RESISTOR, European symbol                         
R15          500k                   R-EU_R0603             R0603                  RESISTOR, European symbol                         
R16          270                    R-EU_R0603             R0603                  RESISTOR, European symbol                         
R17          470                    R-EU_R0603             R0603                  RESISTOR, European symbol                         
R18          660                    R-EU_R0603             R0603                  RESISTOR, European symbol                         
R19          1k                     R-EU_R0603             R0603                  RESISTOR, European symbol                         
R20          50k                    R-EU_R0603             R0603                  RESISTOR, European symbol                         
R21          500                    R-EU_R0603             R0603                  RESISTOR, European symbol                         
R22          500                    R-EU_R0603             R0603                  RESISTOR, European symbol                         
R23          50k                    R-EU_R0603             R0603                  RESISTOR, European symbol                         
R24          500                    R-EU_R0603             R0603                  RESISTOR, European symbol                         
R25          500                    R-EU_R0603             R0603                  RESISTOR, European symbol                         
R26          50k                    R-EU_R0603             R0603                  RESISTOR, European symbol                         
R27          500                    R-EU_R0603             R0603                  RESISTOR, European symbol                         
R28          10k                    R-EU_R0603             R0603                  RESISTOR, European symbol                         
R29          50k                    R-EU_R0603             R0603                  RESISTOR, European symbol                         
R30          33k                    R-EU_R0603             R0603                  RESISTOR, European symbol                         
R31          500                    R-EU_R0603             R0603                  RESISTOR, European symbol                         
R32          10k                    R-EU_R0603             R0603                  RESISTOR, European symbol                         
R33          33k                    R-EU_R0603             R0603                  RESISTOR, European symbol                         
R34          330                    R-EU_R0603             R0603                  RESISTOR, European symbol                         
R35          330                    R-EU_R0603             R0603                  RESISTOR, European symbol                         
R36          330                    R-EU_R0603             R0603                  RESISTOR, European symbol                         
R37          330                    R-EU_R0603             R0603                  RESISTOR, European symbol                         
R38          330                    R-EU_R0603             R0603                  RESISTOR, European symbol                         
R39          330                    R-EU_R0603             R0603                  RESISTOR, European symbol                         
R40          330                    R-EU_R0603             R0603                  RESISTOR, European symbol                         
R41          330                    R-EU_R0603             R0603                  RESISTOR, European symbol                         
R42          330                    R-EU_R0603             R0603                  RESISTOR, European symbol                         
R43          330                    R-EU_R0603             R0603                  RESISTOR, European symbol                         
R44          33k                    R-EU_R0603             R0603                  RESISTOR, European symbol                         
R45          330                    R-EU_R0603             R0603                  RESISTOR, European symbol                         
R46          330                    R-EU_R0603             R0603                  RESISTOR, European symbol                         
R47          22k                    R-EU_R0603             R0603                  RESISTOR, European symbol                         
R48          330                    R-EU_R0603             R0603                  RESISTOR, European symbol                         
R49          330                    R-EU_R0603             R0603                  RESISTOR, European symbol                         
R50          330                    R-EU_R0603             R0603                  RESISTOR, European symbol                         
R51          330                    R-EU_R0603             R0603                  RESISTOR, European symbol                         
R52          1k                     R-EU_R0603             R0603                  RESISTOR, European symbol                         
R53          330                    R-EU_R0603             R0603                  RESISTOR, European symbol                         
R54          1k                     R-EU_R0603             R0603                  RESISTOR, European symbol                         
R55          330                    R-EU_R0603             R0603                  RESISTOR, European symbol                         
R56          1k                     R-EU_R0603             R0603                  RESISTOR, European symbol                         
R57          330                    R-EU_R0603             R0603                  RESISTOR, European symbol                         
R58          1k                     R-EU_R0603             R0603                  RESISTOR, European symbol                         
R59          330                    R-EU_R0603             R0603                  RESISTOR, European symbol                         
R60          1k                     R-EU_R0603             R0603                  RESISTOR, European symbol                         
R61          330                    R-EU_R0603             R0603                  RESISTOR, European symbol                         
R62          1k                     R-EU_R0603             R0603                  RESISTOR, European symbol                         
R63          330                    R-EU_R0603             R0603                  RESISTOR, European symbol                         
R64          10k                    R-EU_R0603             R0603                  RESISTOR, European symbol                         
R65          10k                    R-EU_R0603             R0603                  RESISTOR, European symbol                         
R66          10k                    R-EU_R0603             R0603                  RESISTOR, European symbol                         
R67          10k                    R-EU_R0603             R0603                  RESISTOR, European symbol                         
R68          1k                     R-EU_R0603             R0603                  RESISTOR, European symbol                         
R69          330                    R-EU_R0603             R0603                  RESISTOR, European symbol                         
R70          1k                     R-EU_R0603             R0603                  RESISTOR, European symbol                         
R71          330                    R-EU_R0603             R0603                  RESISTOR, European symbol                         
R72          1k                     R-EU_R0603             R0603                  RESISTOR, European symbol                         
R73          330                    R-EU_R0603             R0603                  RESISTOR, European symbol                         
R74          1k                     R-EU_R0603             R0603                  RESISTOR, European symbol                         
R75          330                    R-EU_R0603             R0603                  RESISTOR, European symbol                         
R76          120                    R-EU_R0603             R0603                  RESISTOR, European symbol                         
R77          120                    R-EU_R0603             R0603                  RESISTOR, European symbol                         
R78          10k                    R-EU_R0603             R0603                  RESISTOR, European symbol                         
R79          120                    R-EU_R0603             R0603                  RESISTOR, European symbol                         
RS485        JST-SHR-8V             JST-SHR-8V             JST-SHR-08V                                                              
RTC                                 M03LOCK                1X03_LOCK              Header 3                                          
SJ1          SOLDERJUMPERNC2        SOLDERJUMPERNC2        SJ_2S-NOTRACE          Solder Jumper                                     
SJ2          SOLDERJUMPERNC2        SOLDERJUMPERNC2        SJ_2S-NOTRACE          Solder Jumper                                     
SJ3          SOLDERJUMPERNC2        SOLDERJUMPERNC2        SJ_2S-NOTRACE          Solder Jumper                                     
SJ4          SOLDERJUMPERNC2        SOLDERJUMPERNC2        SJ_2S-NOTRACE          Solder Jumper                                     
SJ5          SOLDERJUMPERNC2        SOLDERJUMPERNC2        SJ_2S-NOTRACE          Solder Jumper                                     
STM32        STM32F746VG            STM32F746VG            LQFP_100                                                                 
SWD                                 M06LOCK                1X06_LOCK              Header 6                                          
SWITCHS      MC15-GF-3.81-LR_4      MC15-GF-3.81-LR_4      CON_3.81_LR_4                                                            
U3V3L        TSR_1-2433             TSR_1-24XX             TSR1                                                                     
U5VL         TSR_1-2450             TSR_1-24XX             TSR1                                                                     
U12VL        TSR_1-24120            TSR_1-24XX             TSR1                                                                     
UART                                M05LOCK                1X05_LOCK              Header 5                                          
UCAN         SN65HVD230D            MCP2551                SO-08                  High-Speed CAN Transceiver                        
UMOT         MODULE_DRV8843REV      MODULE_DRV8843REV      MODULE_DRV884X_REV                                                       
URS1         SN65HVD1476-DGS        SN65HVD1476-DGS        MSOP-10
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

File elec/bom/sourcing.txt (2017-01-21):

http://fr.farnell.com/molex/53253-0370/embase-male-2-0mm-3-voies/dp/1756921?ost=MOLEX+53253-0370
http://fr.farnell.com/te-connectivity-amp/1-1634688-6/embase-ci-droite-16-voies/dp/8395934
http://fr.farnell.com/te-connectivity/1776275-2/bornier-sur-ci-droit-2-voies-3/dp/1098611
http://fr.farnell.com/te-connectivity-buchanan/1776275-3/bornier-femelle-26-18awg-3p/dp/2311129
http://fr.farnell.com/avago-technologies/asmb-mtb0-0a3a2/led-rgb-plcc4-surface-noire/dp/2401105

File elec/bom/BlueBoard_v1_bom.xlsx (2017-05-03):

IGREBOT 2016
BlueBoard v1 - Bill Of Materials |  |  | Nov. 2015
Device | Package | Value | Qty | Parts | Farnell | Digikey | P.U. | Total |  |  |  | Achats 2017 | Stock | Panier | Nb
ASMB-MTB0-0A3A2 | PLCC4 | ASMB-MTB0-0A3A2 | 1 | LED1 | 2401105 |  | 0.23 € | 0.23 € | X |  |  | OK | 2
C-EUC0603 | C0603 | 100nF | 15 | C1, C4, C5, C6, C7, C8, C28, C29, C32, C35, C37, C43, C44, C45, C46 |  |  |  | 0.00 € | X | +2 |  | OK | 35
C-EUC0603 | C0603 | 10nF | 2 | C9, C10 |  |  |  | 0.00 € | X | +2 |  | OK | 8
C-EUC0603 | C0603 | 18 pF | 2 | C2, C3 |  |  |  | 0.00 € | X |  |  | OK | 8
C-EUC0603 | C0603 | 220nF | 4 | C39, C40, C41, C42 |  |  |  | 0.00 € | X |  |  | OK | 6
C-EUC0603 | C0603 | 3.3nF | 6 | C30, C31, C33, C34, C36, C38 |  |  |  | 0.00 € | X |  |  |  | 4 |  |  | remplacé
C-EUC0805 | C0805 | 1uF | 1 | C11 |  |  |  | 0.00 € | X |  |  | OK | 1
C-EUC0805 | C0805 | 2.2uF | 2 | C12, C13 |  |  |  | 0.00 € | X |  |  | OK | 3 | OK | 20
C-EUC1210 | C1210 | 22uF | 3 | C25, C26, C27 |  |  |  | 0.00 € | X |  |  | OK | 5
C-EUC3225 | C1210 | 2.2uF | 3 | C17, C20, C23 |  |  |  | 0.00 € | X |  |  |  |  | OK | 5
C-EUC3225 | C1210 | 22uF | 4 | C15, C18, C21, C24 |  |  |  | 0.00 € | X |  |  |  |  | OK | 5 | remplacé par 10 uF
CON_1.27_4 | CON_1.27_4 | CON_1.27_4 | 20 | ENC1, ENC2, END1, END2, END3, END4, END5, END6, END7, END8, IND1, IND2, IND3, IND4, IND5, IND6, IND7, IND8, IND9, IND10 | 148507 |  | 0.35 € | 6.96 € | X |  |  |  |  | OK | 20
CON_2.00_MOLEX-53253_3 | CON_2.00_MOLEX-53253_3 | CON_2.00_MOLEX-53253_3 | 2 | DSV1, DSV2 | 1756921 |  | 0.16 € | 0.33 € | X |  |  | OK | 7
CON_3.5_2 | CON_3.5_2 | CON_3.5_2 | 8 | MOT1, MOT2, VCC1, VCC2, VCC3, VP1, VP2, VP3 | 1098611 |  | 0.26 € | 2.06 € | X |  |  |  |  | OK | 10
CON_3.5_3 | CON_3.5_3 | CON_3.5_3 | 9 | ASV1, ASV2, ASV3, ASV4, ASV5, ASV6, ASV7, ASV8, DSV3 | 3882627 |  | 0.39 € | 3.53 € | X |  |  |  |  | OK | 10
CPOL-EUB | PANASONIC_B | 22uF | 1 | C14 | 1868413 |  | 0.31 € | 0.31 € | X |  |  | OK | 4
CPOL-EUD | PANASONIC_D | 220uF | 3 | C16, C19, C22 | 2326116 |  | 0.42 € | 1.26 € | X | +2 |  | OK | 7
DR1030 | DR1030 | 2.8uH | 3 | L1, L2, L3 | 2145102 |  | 0.12 € | 0.37 € | X |  |  |  | 2 | OK | 1
EL3H4-G | SSOP_4 | EL3H4-G | 10 | OPTO9, OPTO10, OPTO11, OPTO12, OPTO13, OPTO14, OPTO15, OPTO16, OPTO17, OPTO18 | 1852698 |  | 0.23 € | 2.29 € | X |  |  |  |  | OK | 10
EL3H7-G | SSOP_4 | HMHA2801R2 | 8 | OPTO1, OPTO2, OPTO3, OPTO4, OPTO5, OPTO6, OPTO7, OPTO8 | 2453214 |  | 0.36 € | 2.88 € | X |  |  |  |  | OK | 10
HE10_V_16 | CON_2X_2.54_V_16 | HE10_V_16 | 1 | HMI | 1554029 |  | 1.14 € | 1.14 € | X |  |  |  |  | OK | 2
INA138 | DBV_05 | INA138 | 4 | IBAT, IP1, IP2, IP3 | Sample |  |  | 0.00 € | X |  |  |  |  | KO | 1 | SAMPLE TODO
JST-SHR-8V | JST-SHR-08V | JST-SHR-8V | 1 | RS485 | 1679134 |  | 0.99 € | 0.99 € | X |  | +9 | OK | 9
JST-XH-S_5 | JST-XH-5S | JST-XH-S_5 | 1 | BAT2 | 1516293 |  | 0.29 € | 0.29 € | X |  | +9 | OK | 9
LEDCHIP-LED0805 | CHIP-LED0805 | BLUE | 3 | LED7, LED8, LED9 | 2217974 |  | 0.17 € | 0.52 € | X |  |  | OK | 6
LEDCHIP-LED0805 | CHIP-LED0805 | GREEN | 3 | LED4, LED5, LED6 | 2290331 |  |  |  |  |  |  | KO | 1 | OK | 10 | changement 1716766
LT1990 | S8 | LT1990 | 4 | CEL1, CEL2, CEL3, CEL4 | 1330733 | LT1990CS8#PBF-ND | 3.35 € | 13.40 € | X
REF3030 | SOT23 | REF3030 | 1 | VREF | Sample |  |  | 0.00 € | X |  |  | OK | 4
MC15-GF-3.81-LR_2 | CON_3.81_LR_2 | MC15-GF-3.81-LR_2 | 1 | BAT1 | 2393507 |  | 1.38 € | 1.38 € | X |  |  |  |  | OK | 1 | correspondance: 1792847
MC15-GF-3.81-LR_4 | CON_3.81_LR_4 | MC15-GF-3.81-LR_4 | 1 | SWITCHS | 2393509 |  | 1.83 € | 1.83 € | X |  |  |  |  | OK | 1 | correspondance: 1792849
MINI-USB-32005-201 | 32005-201 | MINI-USB-32005-201 | 1 | USB | 2112375 |  | 1.55 € | 1.55 € | X |  | +1 | OK | 4
MODULE_DRV8843REV | MODULE_DRV884X_REV | MODULE_DRV8843REV | 2 | UMOT | 1098043 |  | 1.18 € | 2.36 € | X |  |  |  |  | OK | 4
MOSFET-NCHANNELBSS138 | SOT23 | BSS138 | 3 | Q1, Q2, Q3 | 9845330 |  | 0.21 € | 0.62 € | X |  |  |  | 2 | OK | 10
OPA4340U | SO14 | OPA4340U | 2 | OPA1, OPA2 | Sample |  |  | 0.00 € | X |  |  | OK | 2
PTN78060H | PTN78060 | PTN78060H | 1 | UVP3 | 2323482 |  | 21.38 € | 21.38 € |  |  |  | MODULE PRINCE |  |  |  | appro x2
PTN78060W | PTN78060 | PTN78060W | 2 | UVP1, UVP2 |  | 296-20523-ND | 18.51 € | 37.02 € |  |  |  | OK | 2
R-EU_R2512 | R2512 | R005 | 1 | R5 |  |  |  | 0.00 € | X |  |  | OK | 3
R-EU_R2512 | R2512 | R01 | 3 | R6, R10, R13 | 2116438 |  |  | 0.00 € | X |  |  |  | 2 | OK | 5
R-EU_R0603 | R0603 | 47 | 2 | R2, R3 |  |  |  | 0.00 € | X |  |  | OK | 98
R-EU_R0603 | R0603 | 120 | 3 | R76, R77, R79 |  |  |  | 0.00 € | X |  |  | OK
R-EU_R0603 | R0603 | 270 | 4 | R1, R16, R80, R81 |  |  |  | 0.00 € | X |  |  | OK
R-EU_R0603 | R0603 | 330 | 26 | R34, R35, R36, R37, R38, R39, R40, R41, R42, R43, R45, R46, R48, R49, R50, R51, R53, R55, R57, R59, R61, R63, R69, R71, R73, R75 |  |  |  | 0.00 € | X |  |  | OK | 70
R-EU_R0603 | R0603 | 470 | 7 | R17, R21, R22, R24, R25, R27, R31 |  |  |  | 0.00 € | X |  |  | OK | 100
R-EU_R0603 | R0603 | 680 | 1 | R18 |  |  |  | 0.00 € | X |  |  | OK | 9
R-EU_R0603 | R0603 | 1k | 11 | R19, R52, R54, R56, R58, R60, R62, R68, R70, R72, R74 |  |  |  | 0.00 € | X |  |  | OK
R-EU_R0603 | R0603 | 7.5k | 1 | R11 |  |  |  | 0.00 € | X |  |  | OK
R-EU_R0603 | R0603 | 10k | 7 | R28, R32, R64, R65, R66, R67, R78 |  |  |  | 0.00 € | X |  |  | OK | 90
R-EU_R0603 | R0603 | 21k | 2 | R8, R47 |  |  |  | 0.00 € | X |  |  | OK
R-EU_R0603 | R0603 | 33k | 3 | R30, R33, R44 |  |  |  | 0.00 € | X |  |  | OK
R-EU_R0603 | R0603 | 47k | 8 | R4, R20, R23, R26, R29, R82, R83, R84 |  |  |  | 0.00 € | X |  |  | OK
R-EU_R0603 | R0603 | 300k | 1 | R7 |  |  |  | 0.00 € | X |  |  | OK
R-EU_R0603 | R0603 | 383k | 1 | R14 |  |  |  | 0.00 € | X |  |  | OK
R-EU_R0603 | R0603 | 510k | 3 | R9, R12, R15 |  |  |  | 0.00 € | X |  |  | OK | 47
R-TRIMMT93XB | RTRIMT93XB | 50k | 1 | P1 | 1141392 |  | 1.59 € | 1.59 € | X |  |  |  |  | OK | 1
SN65HVD1476-DGS | MSOP-10 | SN65HVD1476-DGS | 1 | URS485 | Sample |  |  | 0.00 € | X |  |  | OK | 4
SN65HVD230D | SO-08 | SN65HVD230D | 1 | UCAN | Sample |  |  | 0.00 € | X |  |  | OK | 4
STM32F746VG | LQFP_100 | STM32F746VG | 1 | STM32 | 2484971 | 497-15819-ND | 15.86 € | 15.86 € | X |  |  | OK | 2
TSR_1-24XX | TSR1 | TSR_1-24120 | 1 | U12VL | 1672130 |  | 5.50 € | 5.50 € | X |  |  | OK | 2
TSR_1-24XX | TSR1 | TSR_1-2433 | 1 | U3V3L | 1696319 |  | 7.10 € | 7.10 € | X |  |  | OK | 2
TSR_1-24XX | TSR1 | TSR_1-2450 | 1 | U5VL | 1696320 |  | 4.40 € | 4.40 € | X |  |  | OK | 2
XTAL_5X3 | CRYSTAL-OSC-SMD-5X3 | XTAL_5X3 | 1 | CX1 | 2308726 |  | 1.43 € | 1.43 € | X |  |  |  |  | OK | 2
 |  |  |  |  |  |  | Total: | 138.58 €
 |  |  |  |  |  |  | Shipping: | 12.00 €
 |  |  |  |  |  |  | VAT: | 30.12 €
 |  |  |  |  |  |  | Grand Total: | 168.70 €
R52 | 1k | R-EU_R0603 | R0603
R53 | 330 | R-EU_R0603 | R0603
R54 | 1k | R-EU_R0603 | R0603
R55 | 330 | R-EU_R0603 | R0603
R56 | 1k | R-EU_R0603 | R0603
R57 | 330 | R-EU_R0603 | R0603
R58 | 1k | R-EU_R0603 | R0603
R59 | 330 | R-EU_R0603 | R0603
R60 | 1k | R-EU_R0603 | R0603
R61 | 330 | R-EU_R0603 | R0603
R62 | 1k | R-EU_R0603 | R0603
R63 | 330 | R-EU_R0603 | R0603
R64 | 10k | R-EU_R0603 | R0603
R65 | 10k | R-EU_R0603 | R0603
R66 | 10k | R-EU_R0603 | R0603
R67 | 10k | R-EU_R0603 | R0603
R68 | 1k | R-EU_R0603 | R0603
R69 | 330 | R-EU_R0603 | R0603
R70 | 1k | R-EU_R0603 | R0603
R71 | 330 | R-EU_R0603 | R0603
R72 | 1k | R-EU_R0603 | R0603
R73 | 330 | R-EU_R0603 | R0603
R74 | 1k | R-EU_R0603 | R0603
R75 | 330 | R-EU_R0603 | R0603
R76 | 120 | R-EU_R0603 | R0603
R77 | 120 | R-EU_R0603 | R0603
R78 | 10k | R-EU_R0603 | R0603
R79 | 120 | R-EU_R0603 | R0603
RS485 | JST-SHR-8V | JST-SHR-8V | JST-SHR-08V
RTC |  | M03LOCK | 1X03_LOCK
STM32 | STM32F746VG | STM32F746VG | LQFP_100
SWD |  | M06LOCK | 1X06_LOCK
SWITCHS | MC15-GF-3.81-LR_4 | MC15-GF-3.81-LR_4 | CON_3.81_LR_4
U3V3L | TSR_1-2433 | TSR_1-24XX | TSR1
U5VL | TSR_1-2450 | TSR_1-24XX | TSR1
U12VL | TSR_1-24120 | TSR_1-24XX | TSR1
UART |  | M05LOCK | 1X05_LOCK
UCAN | SN65HVD230D | MCP2551 | SO-08
UMOT | MODULE_DRV8843REV | MODULE_DRV8843REV | MODULE_DRV884X_REV
URS485 | SN65HVD1476-DGS | SN65HVD1476-DGS | MSOP-10
USB | MINI-USB-32005-201 | MINI-USB-32005-201 | 32005-201
UVP1 | PTN78060W | PTN78060W | PTN78060
UVP2 | PTN78060W | PTN78060W | PTN78060
UVP3 | PTN78020H | PTN78060W | PTN78060
VCC1 | CON_3.5_2 | CON_3.5_2 | CON_3.5_2
VCC2 | CON_3.5_2 | CON_3.5_2 | CON_3.5_2
VCC3 | CON_3.5_2 | CON_3.5_2 | CON_3.5_2
VP1 | CON_3.5_2 | CON_3.5_2 | CON_3.5_2
VP2 | CON_3.5_2 | CON_3.5_2 | CON_3.5_2
VP3 | CON_3.5_2 | CON_3.5_2 | CON_3.5_2
VREF | REF3030 | MAX6520 | SOT23

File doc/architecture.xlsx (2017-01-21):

 |  |  |  | Required I/O |  | Mapping per device |  |  |  |  |  |  | Schematic Status
Resource | Count | Details | Peripheral per item | Per item | Total | µC Main |  | FPGA Main |  | µc HMI
Cells voltage monitoring | 6 | 1 ADC channel per LiPo cell | 1 ADC channel | 1 | 6 | 6 | 6 |  | 0 |  | 0 | 0
Current sensing | 6 | 1 ADC channel per shunt sensing | 1 ADC channel | 1 | 6 | 6 | 6 |  | 0 |  | 0 | 0
Power supply enable | 4 | 1 ENABLE output | 1 digital output | 1 | 4 | 4 | 4 |  | 0 |  | 0 | 0 | OK
Type A Full H-bridges | 3 | 1 PWM signal 1 DIR signal 1 DECAY signal 1 SLEEP signal 1 FAULT signal 1 SENSE Feedback | 1 PWM channel 4 digital outputs 1 ADC channel | 6 | 18 | 3 | 18 |  | 0 |  | 0 | 0 | OK
Type B Full H-bridges | 8 | 1 PWM signal 1 DIR signal 0,5 DECAY signal 0,5 SLEEP signal 0,5 FAULT signal 1 SENSE Feedback | 1 PWM channels 2.5 digital outputs 1 ADC channel | 4.5 | 36 | 4 | 18 | 4 | 18 |  | 0 | 0 | OK
Common for Full H-bridges | 1 | 1 RESET signal | 1 digital output | 1 | 1 | 1 | 1 |  | 0 |  | 0 | 0 | OK
ON/OFF power mosfets | 16 | 1 ENABLE signal | 1 digital output | 1 | 16 | 16 | 16 |  | 0 |  | 0 | 0 | OK
Analog servos | 8 | 1 PWM signal | 1 PWM channel | 1 | 8 |  | 0 | 8 | 8 |  | 0 | 0 | OK
Digital servos interface | 1 | 1 TX/RX signal 1 DIR signal | 1 UART input 1 UART output 1 digital output | 3 | 3 | 1 | 3 |  | 0 |  | 0 | 0 | OK
NPN/PNP Industrial sensors | 20 | 1 input signal | 1 digital input | 1 | 20 | 20 | 20 |  | 0 |  | 0 | 0 | OK
Endstops | 8 | 1 input signal | 1 digital input | 1 | 8 | 8 | 8 |  | 0 |  | 0 | 0 | OK
Encoders interface | 12 | 1 'A' channel 1 'B' channel 1 '0' channel | 1 QEI channel | 3 | 36 | 2 | 6 | 10 | 30 |  | 0 | 0 | OK
Emergency switch feedback | 1 | 1 input signal | 1 digital input | 1 | 1 |  | 0 |  | 0 | 1 | 1 | 0
Team selection switch | 1 | 1 input signal | 1 digital input | 1 | 1 |  | 0 |  | 0 | 1 | 1 | 0
Start switch or interface | 1 | 1 input signal | 1 digital input | 1 | 1 |  | 0 |  | 0 | 1 | 1 | 0
Spare switch (strategy) | 1 | 1 input signal | 1 digital input | 1 | 1 |  | 0 |  | 0 | 1 | 1 | 0
OLED Display | 1 | 1 CS signal 1 RESET signal 1 D/C signal 1 R/W signal 1 E/RD signal 8 D signals | 1 PMP interface 1 digital output | 13 | 13 |  | 0 |  | 0 | 1 | 13 | 0
OLED Intensity adjustment | 1 | 1 CS signal 1 MOSI signal 1 SCK signal | 1 SPI interface* 1 digital output | 3 | 3 |  | 0 |  | 0 | 1 | 3 | 0
Encoder for menu + Push button | 1 | 1 'A' channel 1 'B' channel 1 push-button input | 3 digital inputs | 3 | 3 |  | 0 |  | 0 | 1 | 3 | 0
RGB LED | 1 | 1 PWM output for Red intensity 1 PWM output for Green intensity 1 PWM output for Blue intensity | 3 PWM channels | 3 | 3 |  | 0 |  | 0 | 1 | 3 | 0
Micro SD interface | 1 | 1 SCK signal 1 MISO signal 1 MOSI signal 1 CS signal | 1 SPI interface* 1 digital output | 4 | 4 |  | 0 |  | 0 | 1 | 4 | 0
Piezo beeper | 1 | 1 PWM signal | 1 PWM channel | 1 | 1 |  | 0 |  | 0 | 1 | 1 | 0
Inter-uc / FPGA communication | 3 | 1 SCK signal 1 MISO signal 1 MOSI signal 1 CS signal | 1 SPI interface* 1 digital output | 4 | 12 | 1 | 4 | 1 | 4 | 1 | 4
Total |  |  |  |  | 193 |  | 110 |  | 60 |  | 35
Available |  |  |  |  | 218 |  | 122 |  | 61 |  | 35
* If multiple slave SPI devices are present, the 3 I/O from the SPI interface can be saved
(only the CS pins need to be duplicated)

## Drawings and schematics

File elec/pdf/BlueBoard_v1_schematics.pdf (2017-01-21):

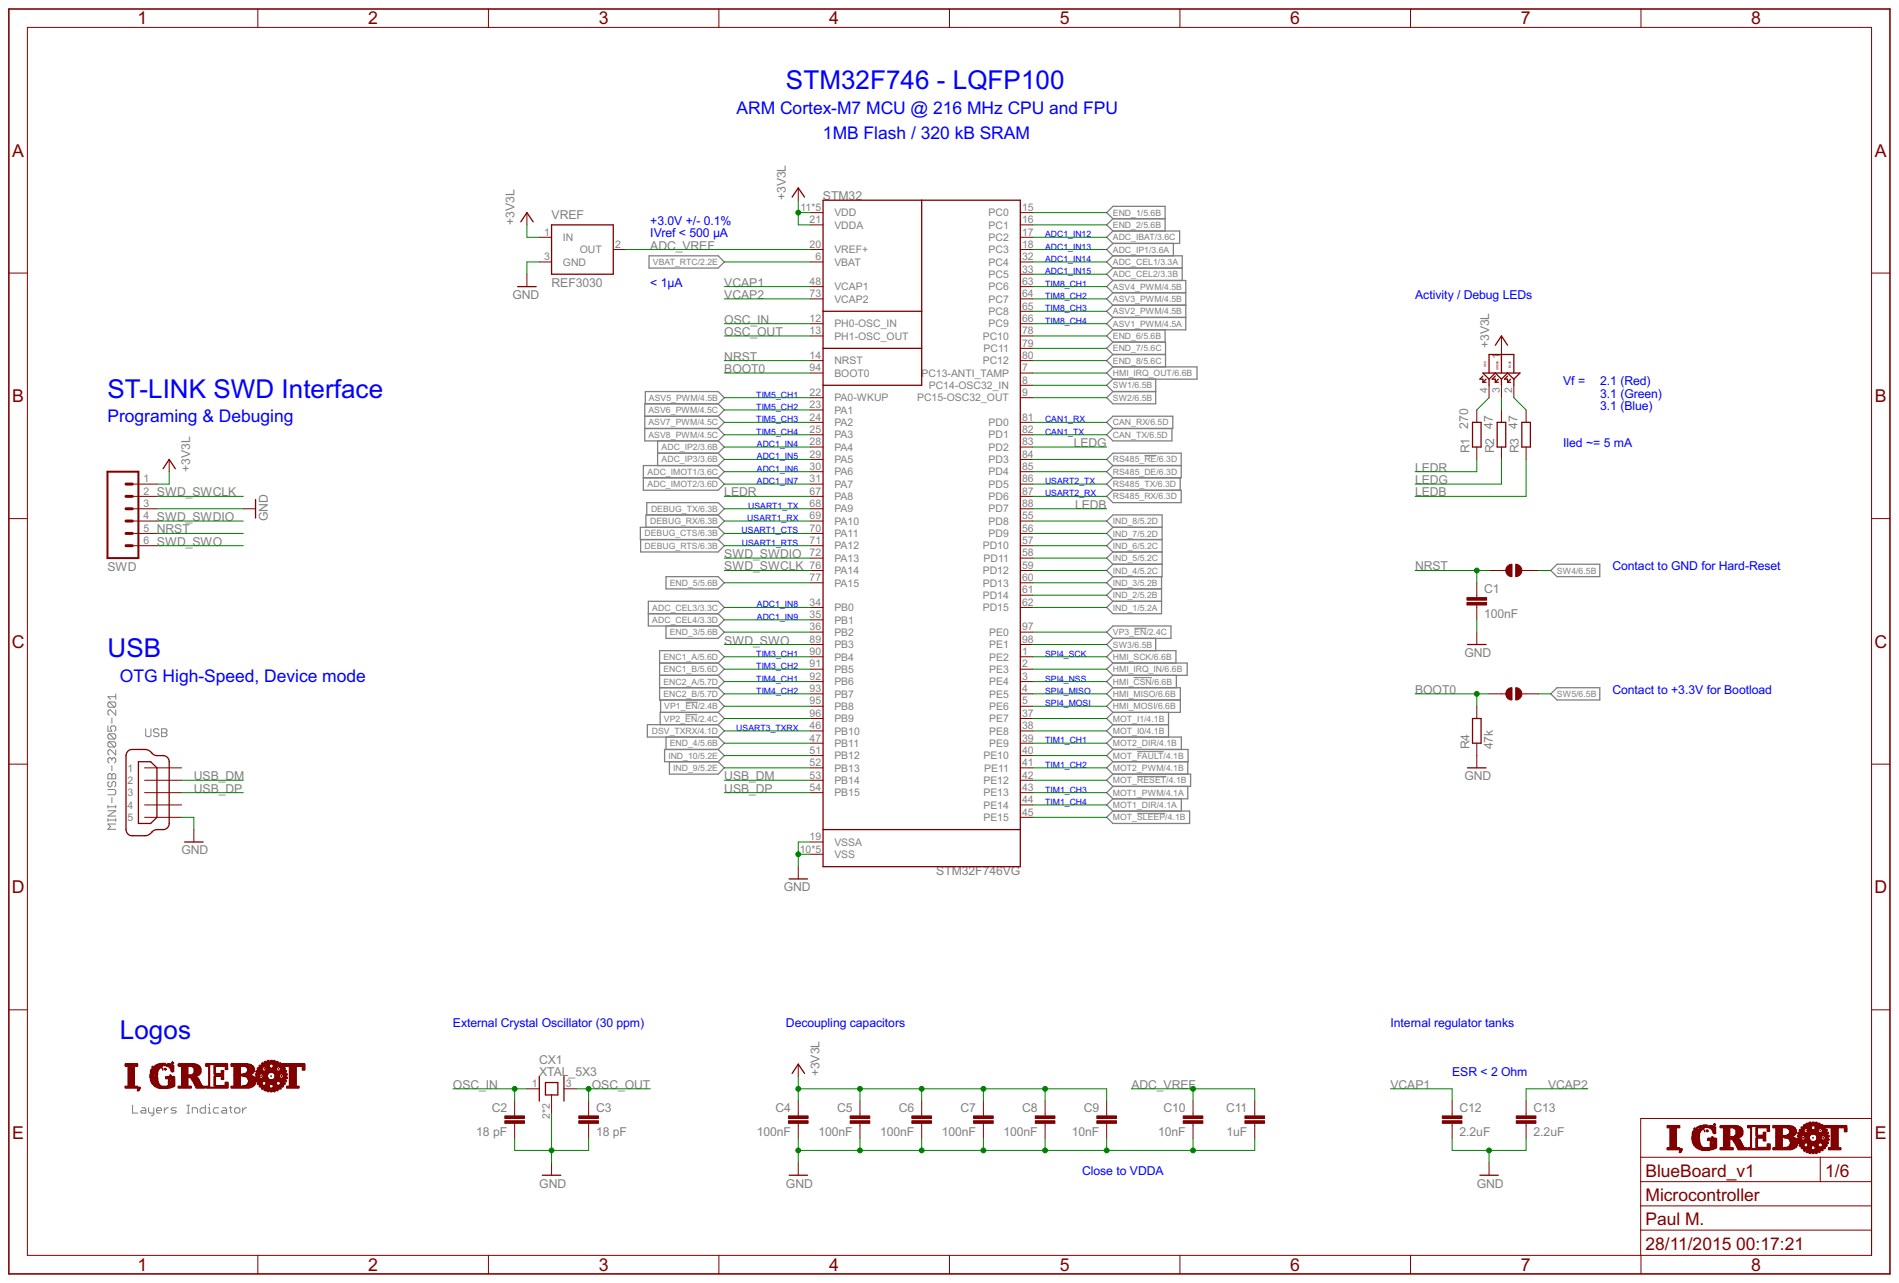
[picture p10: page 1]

STM32F746 - LQFP100
ARM Cortex-M7 MCU @ 216 MHz CPU and FPU

ST-LINK SWD Interface
Programing & Debuging

ASV8_PWM/4.5C | LEDG

31 ADC_IMOT2/3.6D | LEDG

Contact to GND for Hard-Reset

USB
OTG High-Speed, Device mode

ENC1_A/5.6D | 1 SPI4_SCK

Contact to +3.3V for Bootload

ENC2_B/5.7D | 5

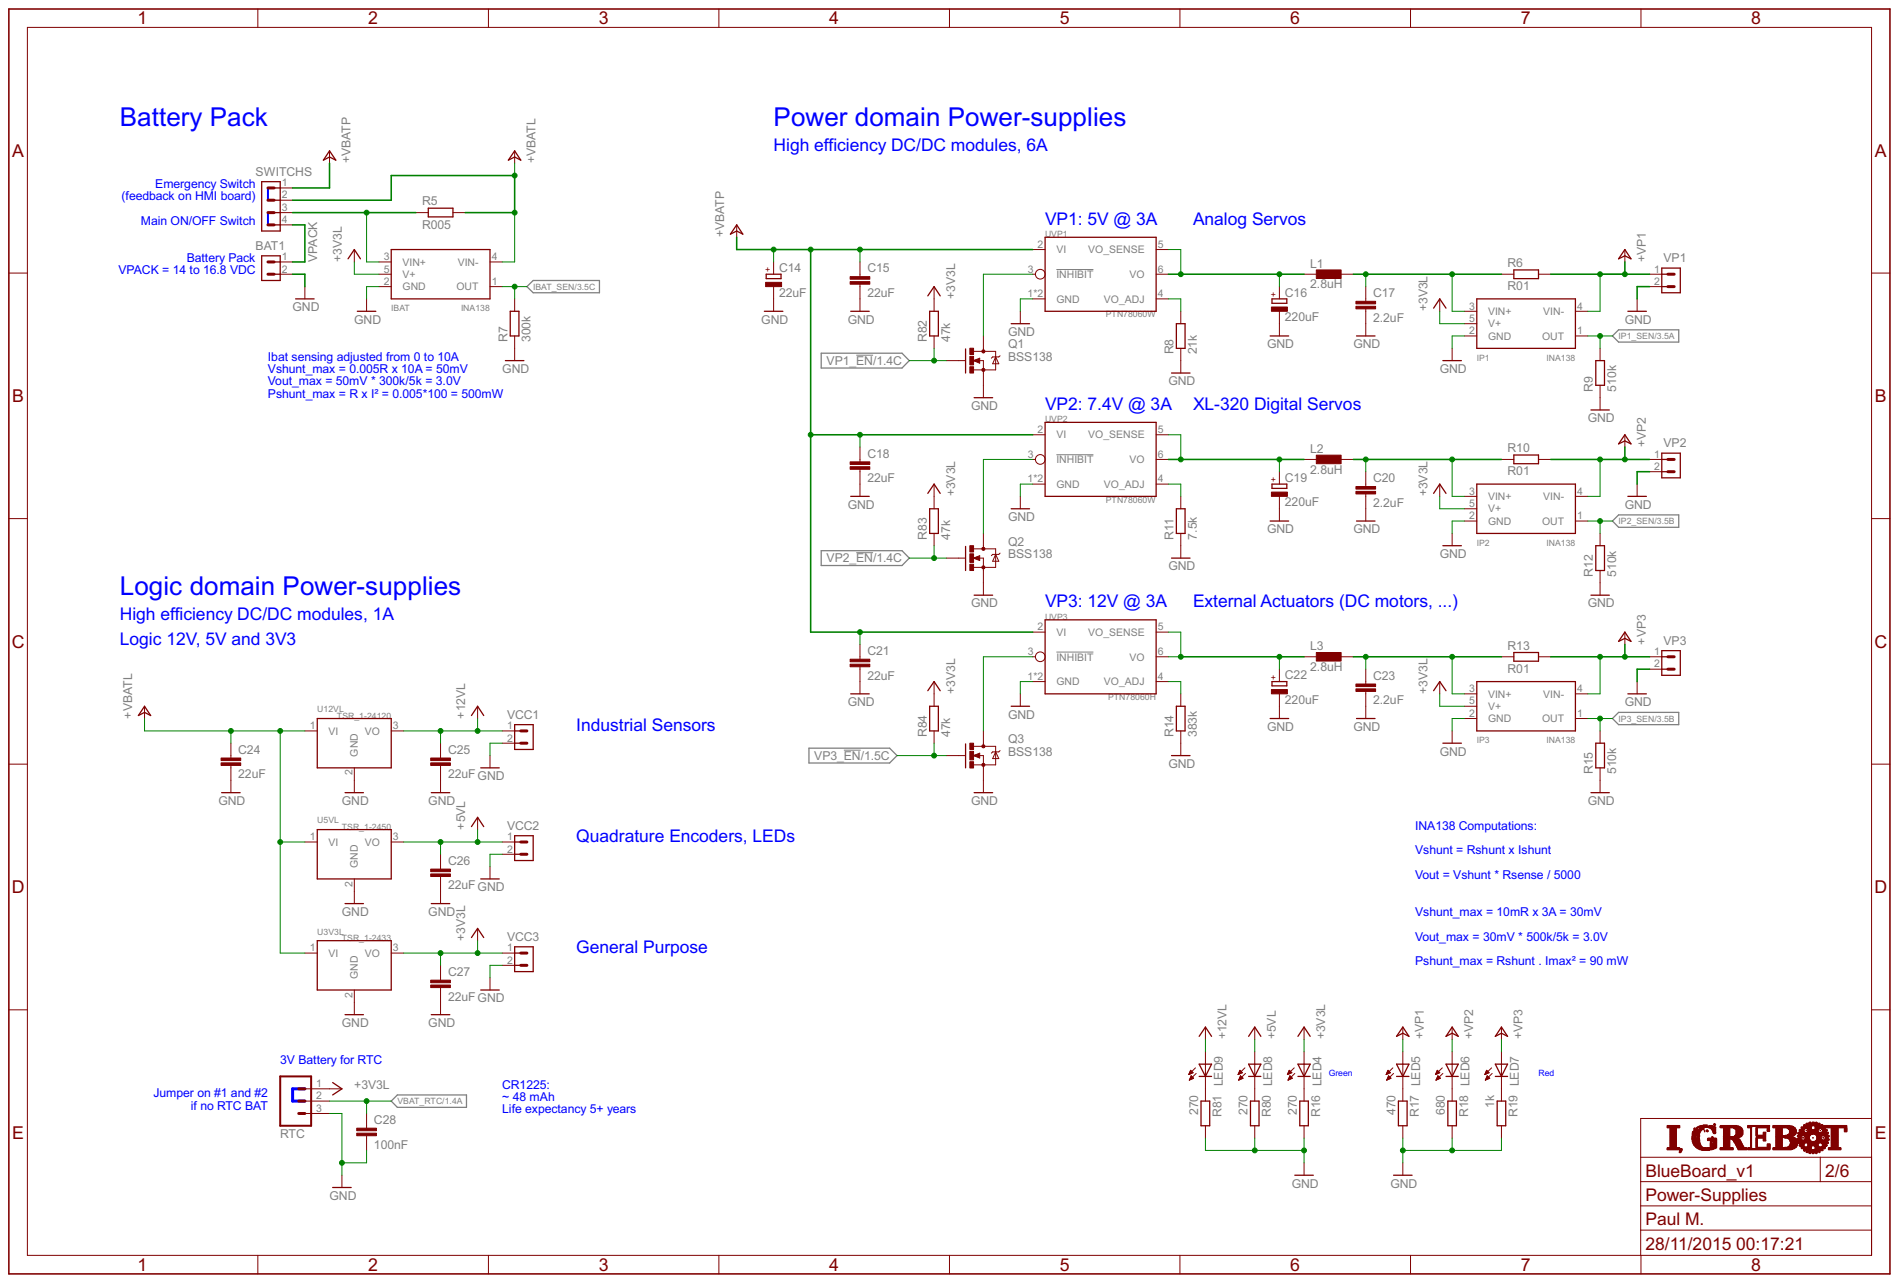
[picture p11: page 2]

Power domain Power-supplies
High efficiency DC/DC modules, 6A

Emergency Switch Main ON/OFF Switch Battery Pack
(feedback on HMI board)

Logic domain Power-supplies
High efficiency DC/DC modules, 1A
Logic 12V, 5V and 3V3

General Purpose Quadrature Encoders, LEDs

Vshunt = Rshunt x Ishunt Vout = Vshunt * Rsense / 5000 Vshunt_max = 10mR x 3A = 30mV

if no RTC BAT

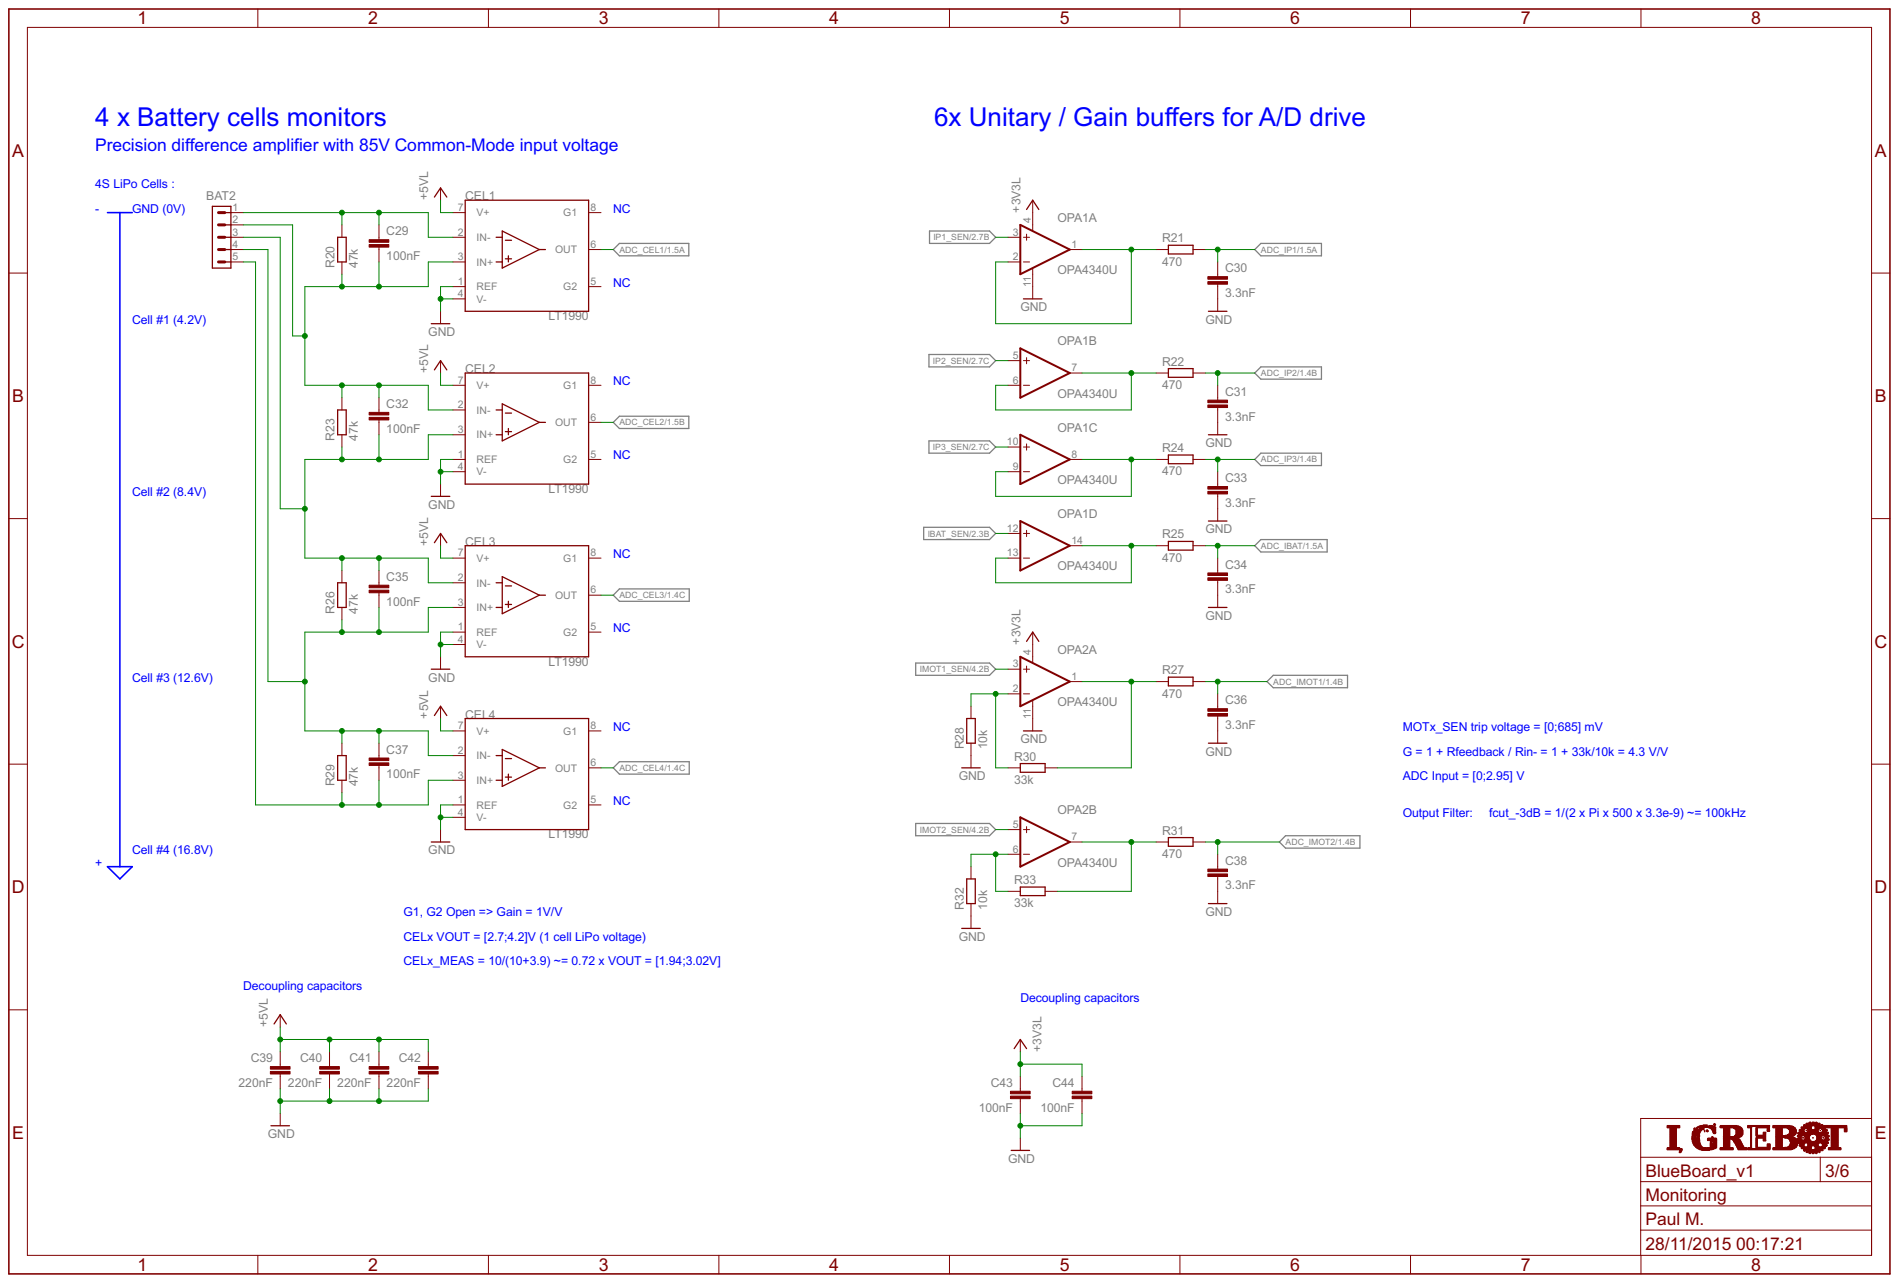
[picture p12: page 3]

-4 x Battery cells monitors
Precision difference amplifier with 85V Common-Mode input voltage

6x Unitary / Gain buffers for A/D drive

GND GND GND OPA4340U GND

fcut_-3dB = 1/(2 x Pi x 500 x 3.3e-9) ~= 100kHz G = 1 + Rfeedback / Rin- = 1 + 33k/10k = 4.3 V/V MOTx_SEN trip voltage = [0;685] mV

G1, G2 Open => Gain = 1V/V CELx VOUT = [2.7;4.2]V (1 cell LiPo voltage) CELx_MEAS = 10/(10+3.9) ~= 0.72 x VOUT = [1.94;3.02V]

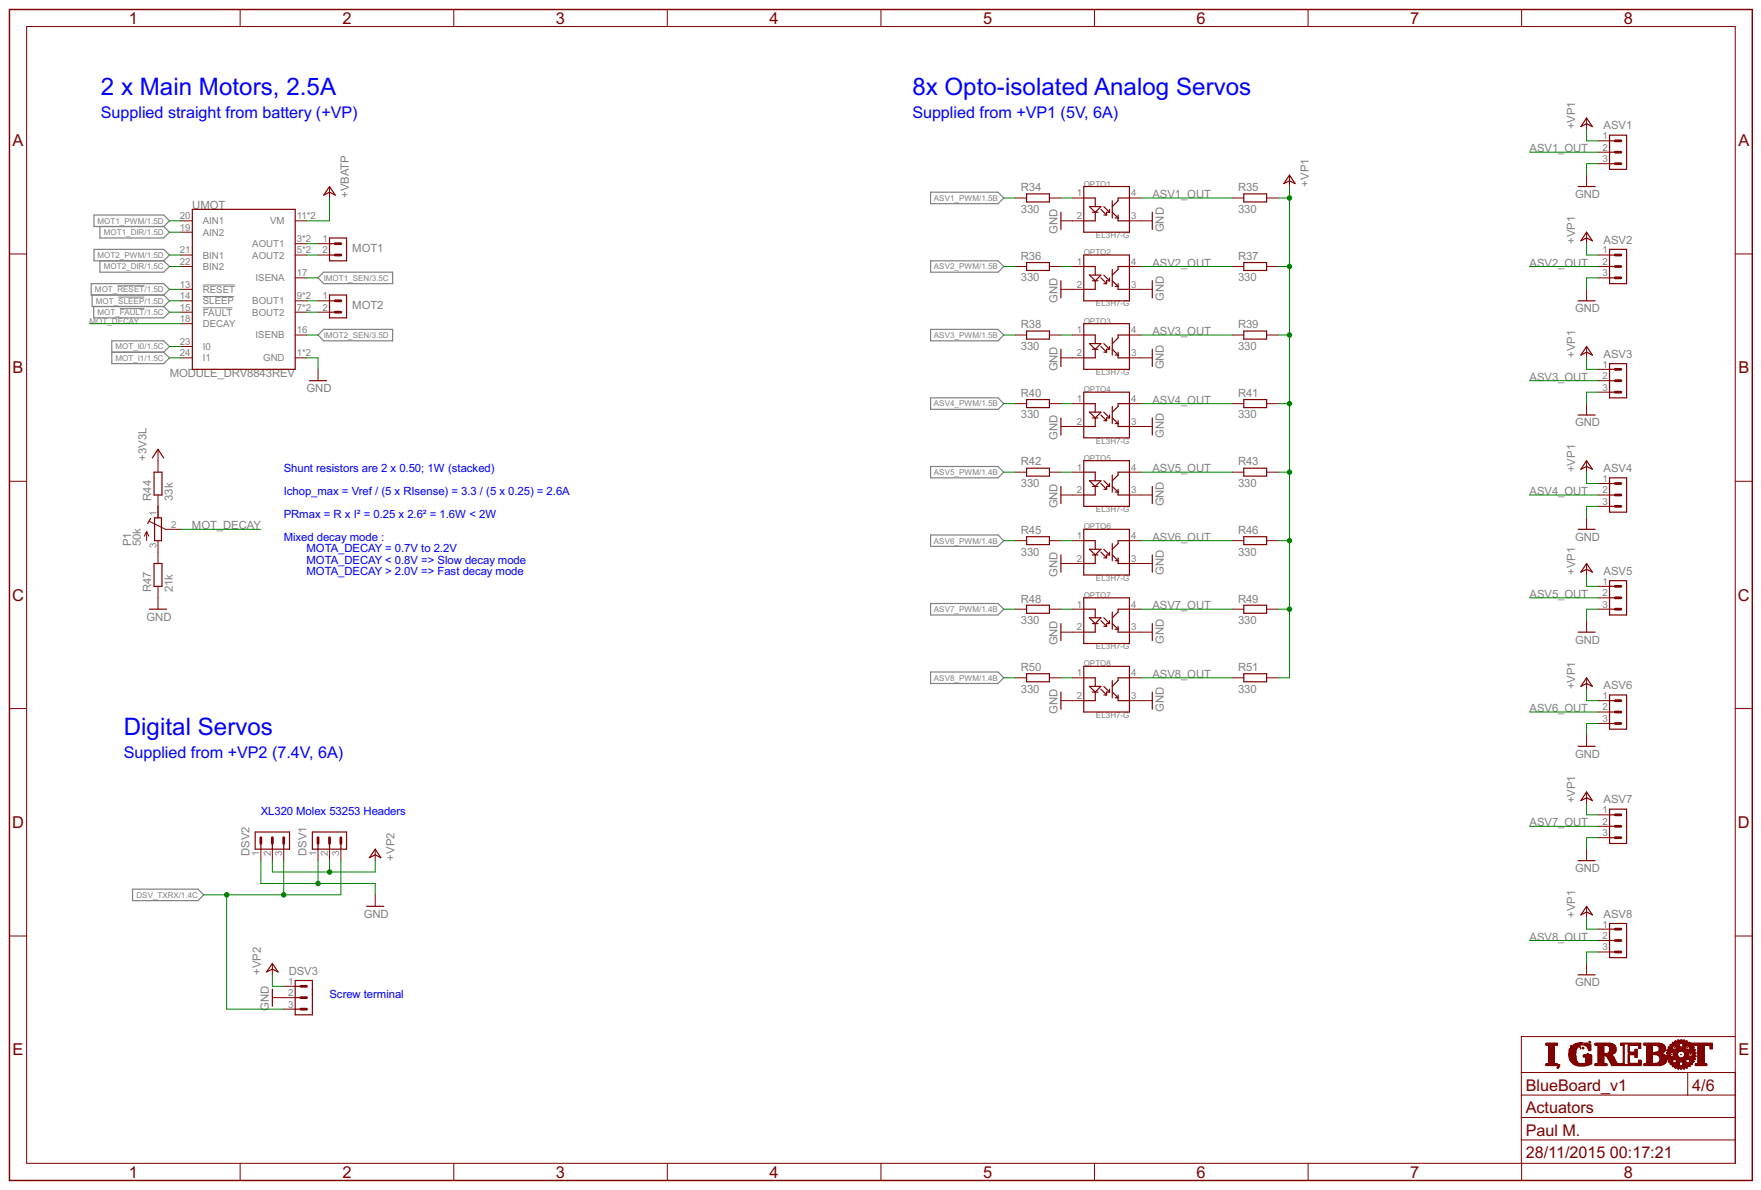
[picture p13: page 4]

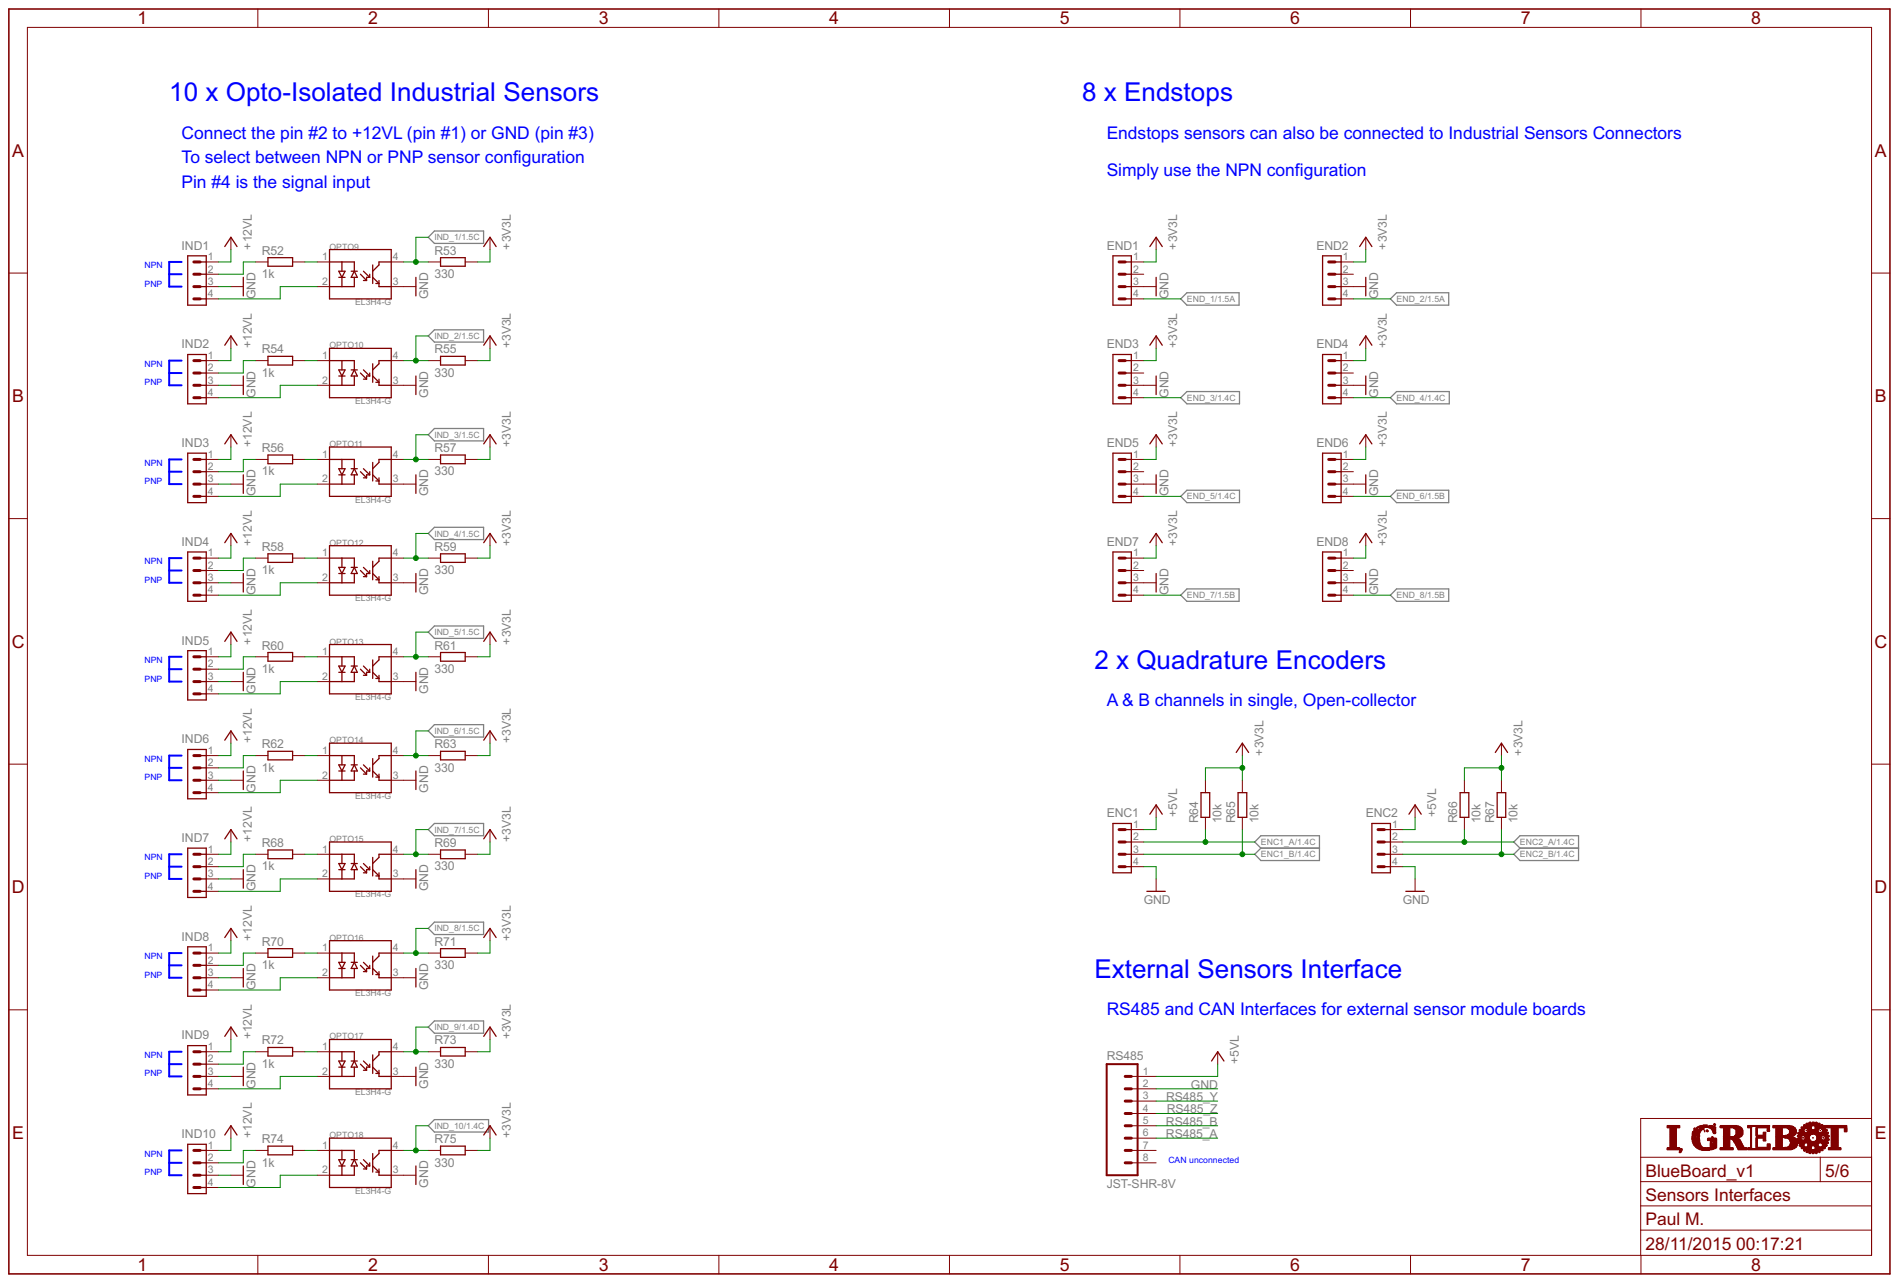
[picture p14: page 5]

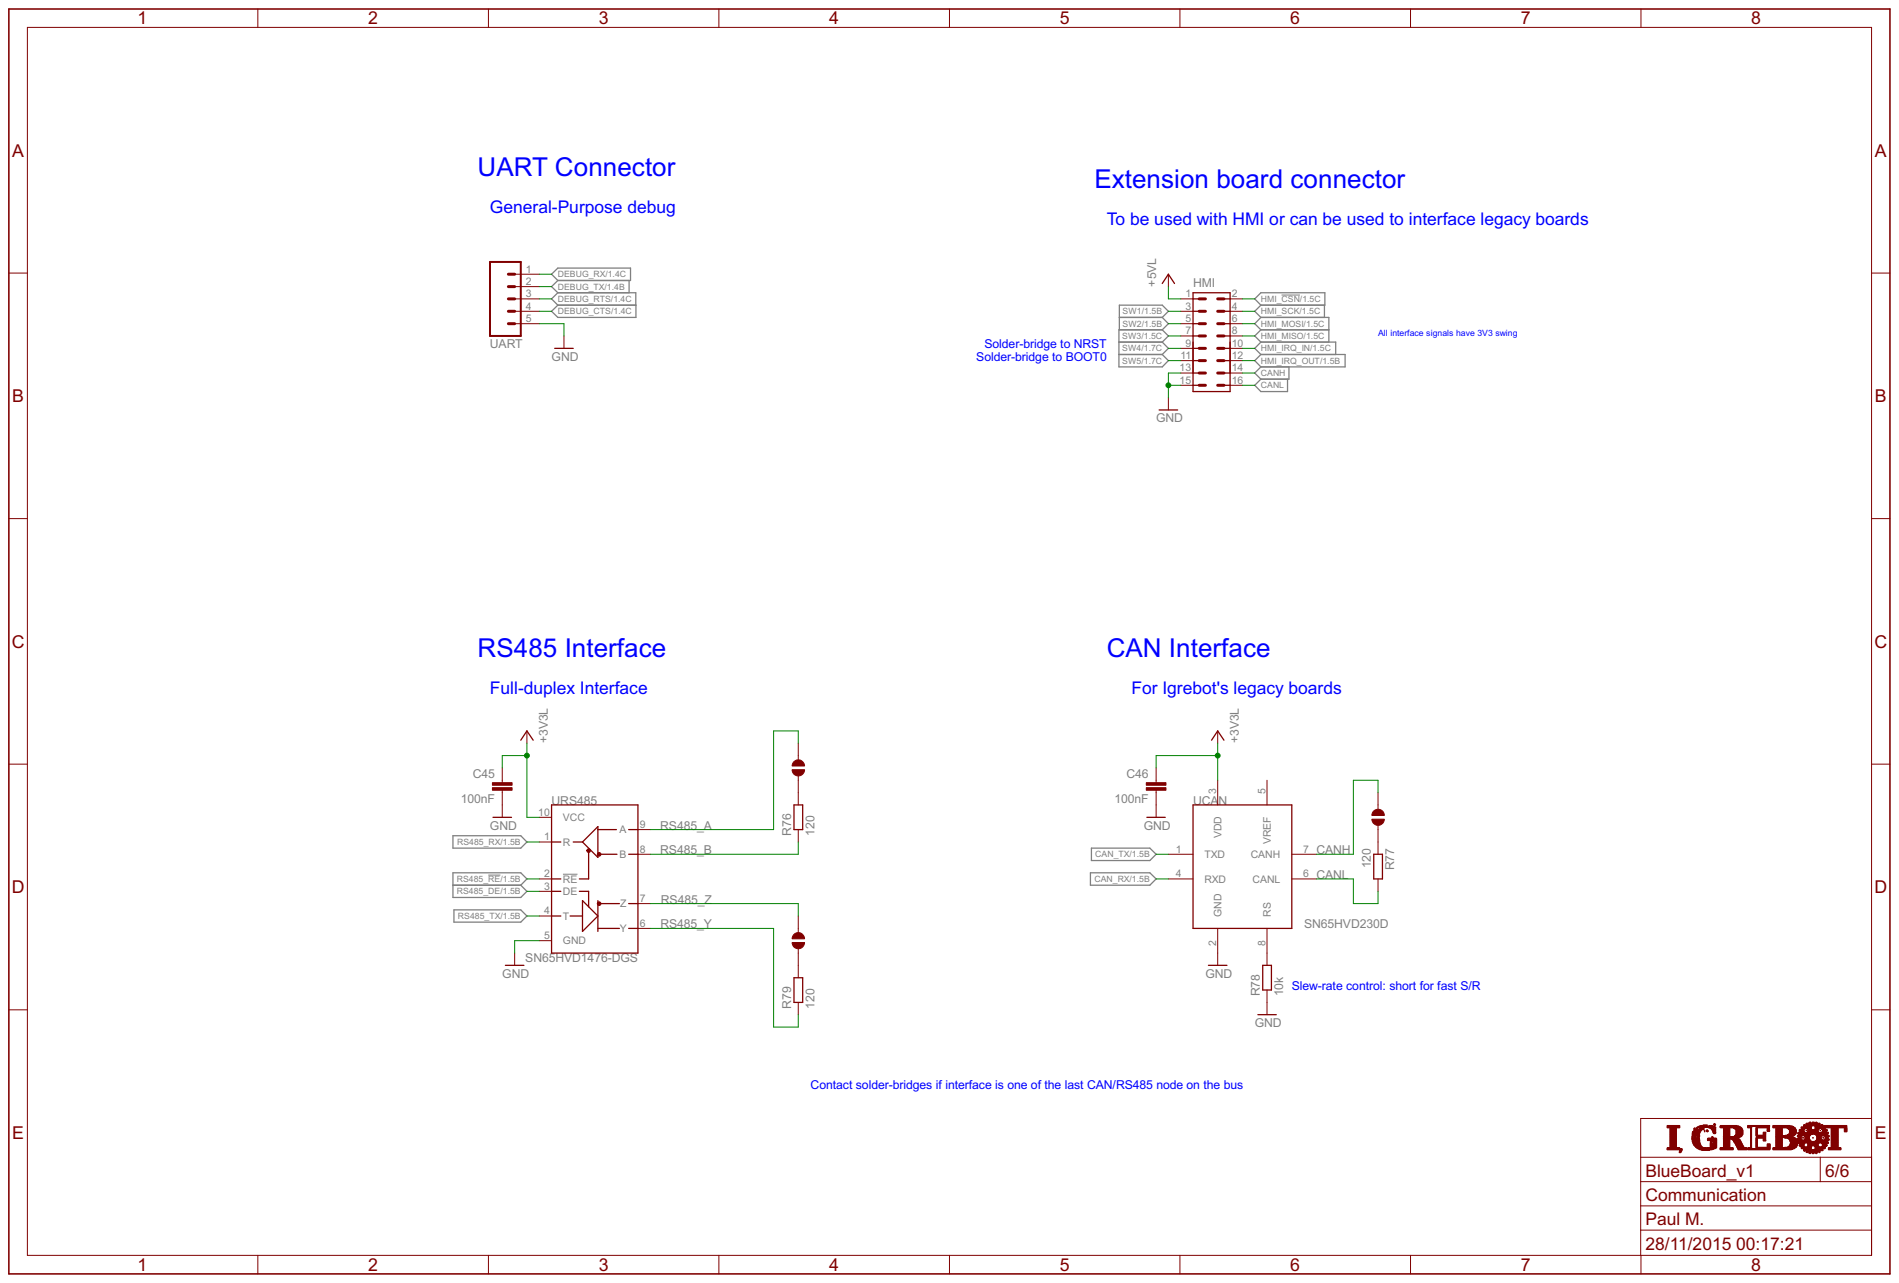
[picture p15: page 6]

To be used with HMI or can be used to interface legacy boards Extension board connector

SW2/1.5B | HMI_MOSI/1.5C
7 SW3/1.5C | HMI_MISO/1.5C
9 SW4/1.7C | HMI_IRQ_IN/1.5C

All interface signals have 3V3 swing Solder-bridge to NRST Solder-bridge to BOOT0

SW5/1.7C 13 | HMI_IRQ_OUT/1.5B

For Igrebot's legacy boards CAN Interface

Slew-rate control: short for fast S/R

Contact solder-bridges if interface is one of the last CAN/RS485 node on the bus

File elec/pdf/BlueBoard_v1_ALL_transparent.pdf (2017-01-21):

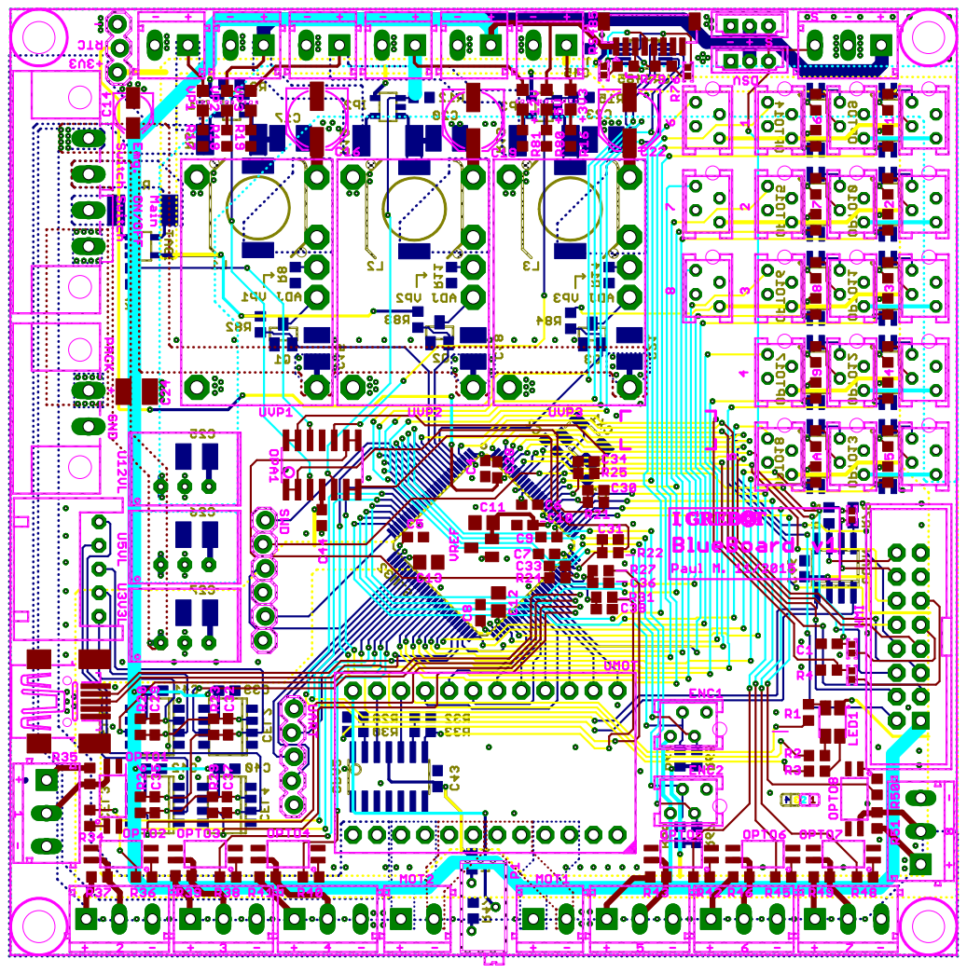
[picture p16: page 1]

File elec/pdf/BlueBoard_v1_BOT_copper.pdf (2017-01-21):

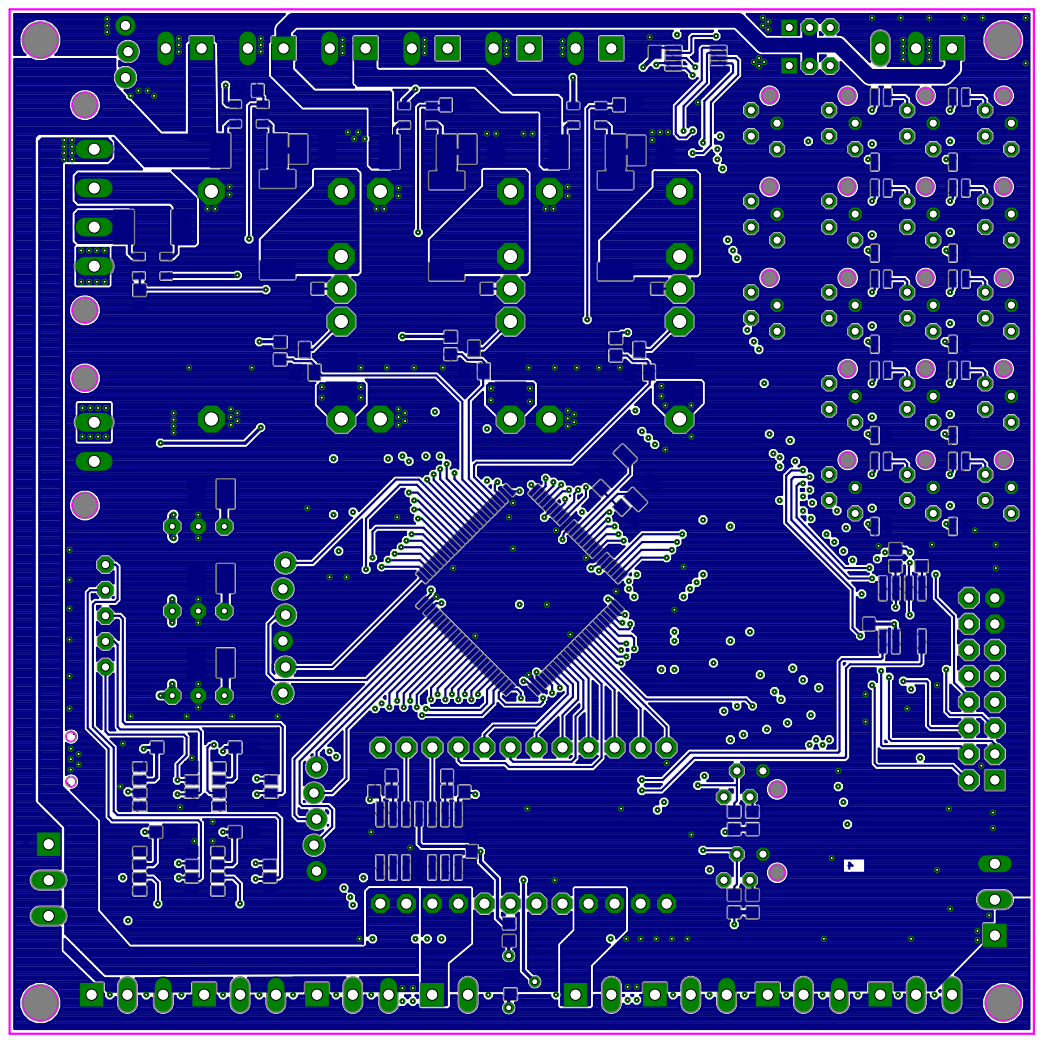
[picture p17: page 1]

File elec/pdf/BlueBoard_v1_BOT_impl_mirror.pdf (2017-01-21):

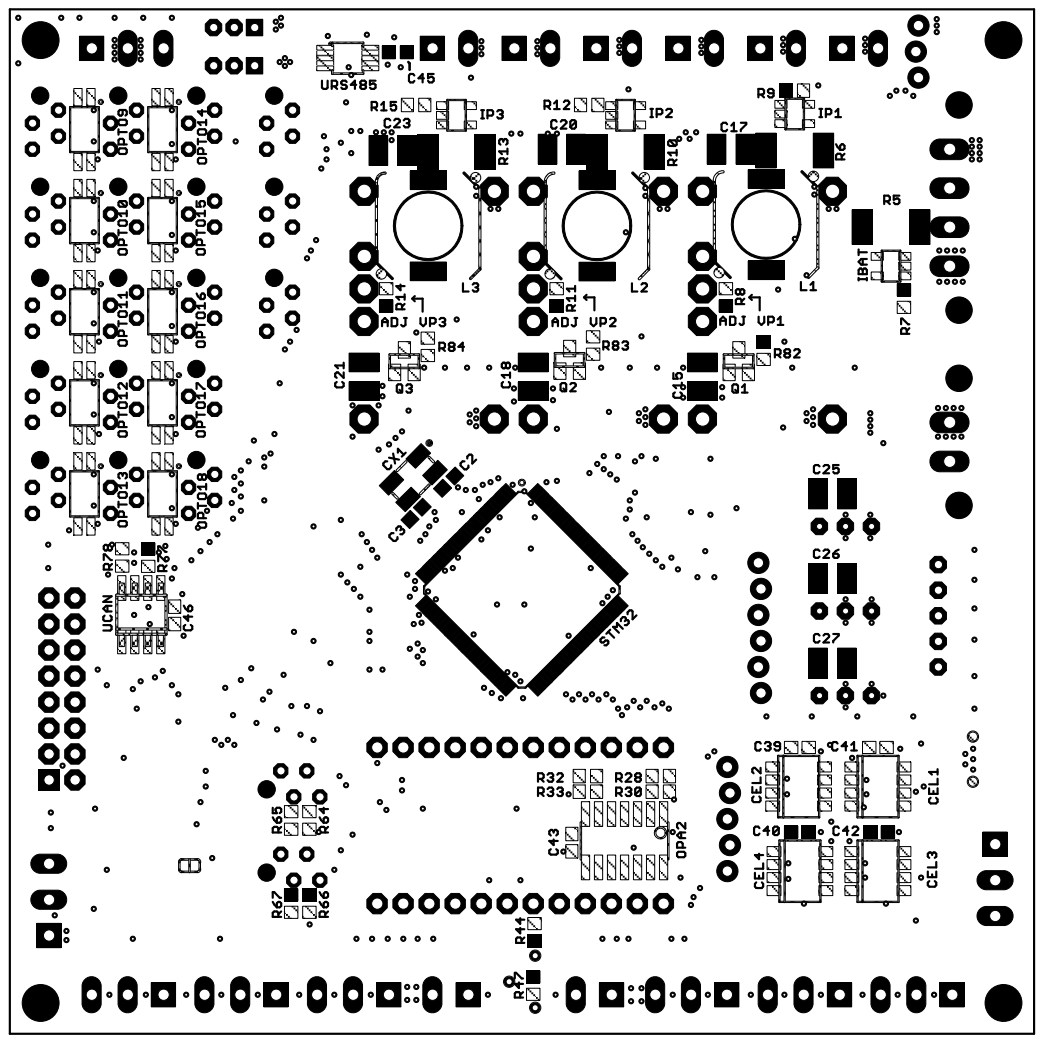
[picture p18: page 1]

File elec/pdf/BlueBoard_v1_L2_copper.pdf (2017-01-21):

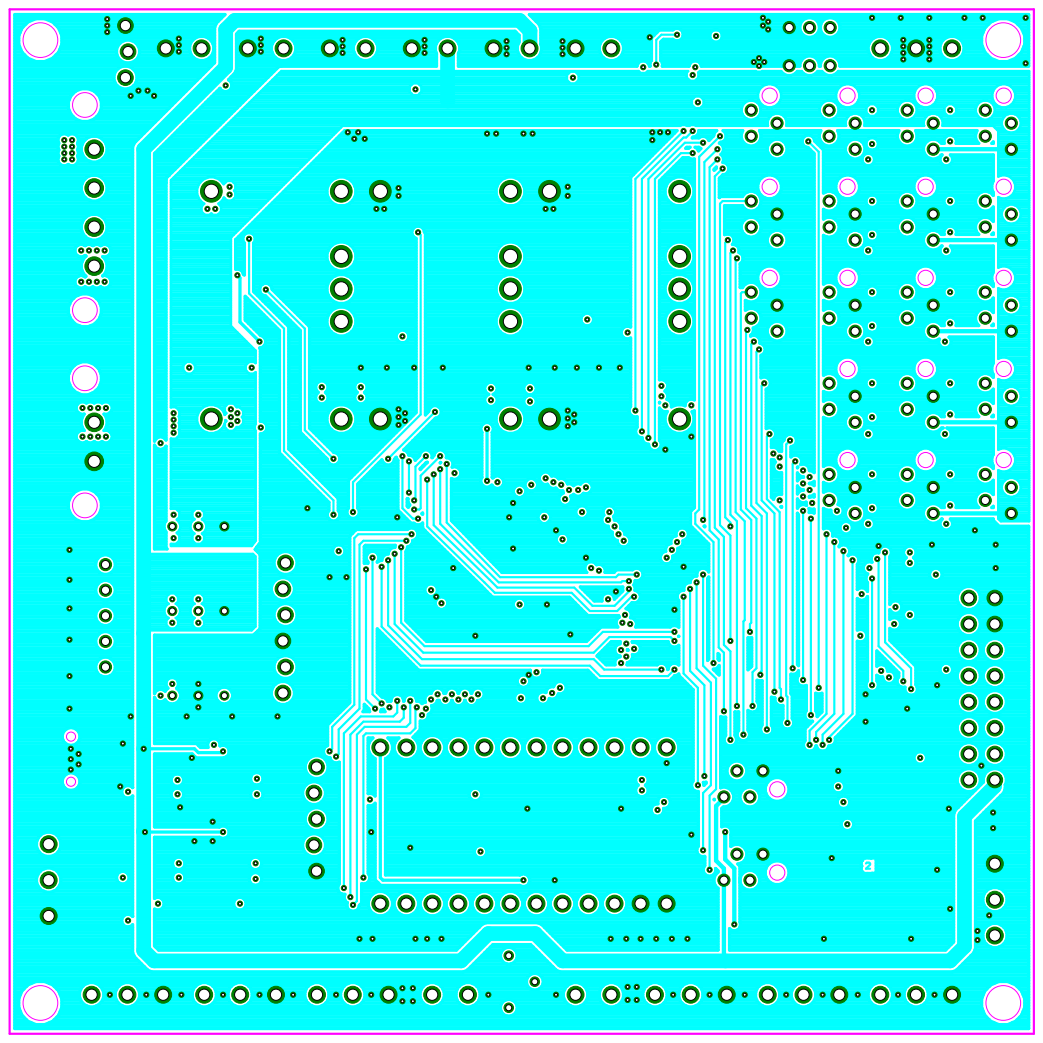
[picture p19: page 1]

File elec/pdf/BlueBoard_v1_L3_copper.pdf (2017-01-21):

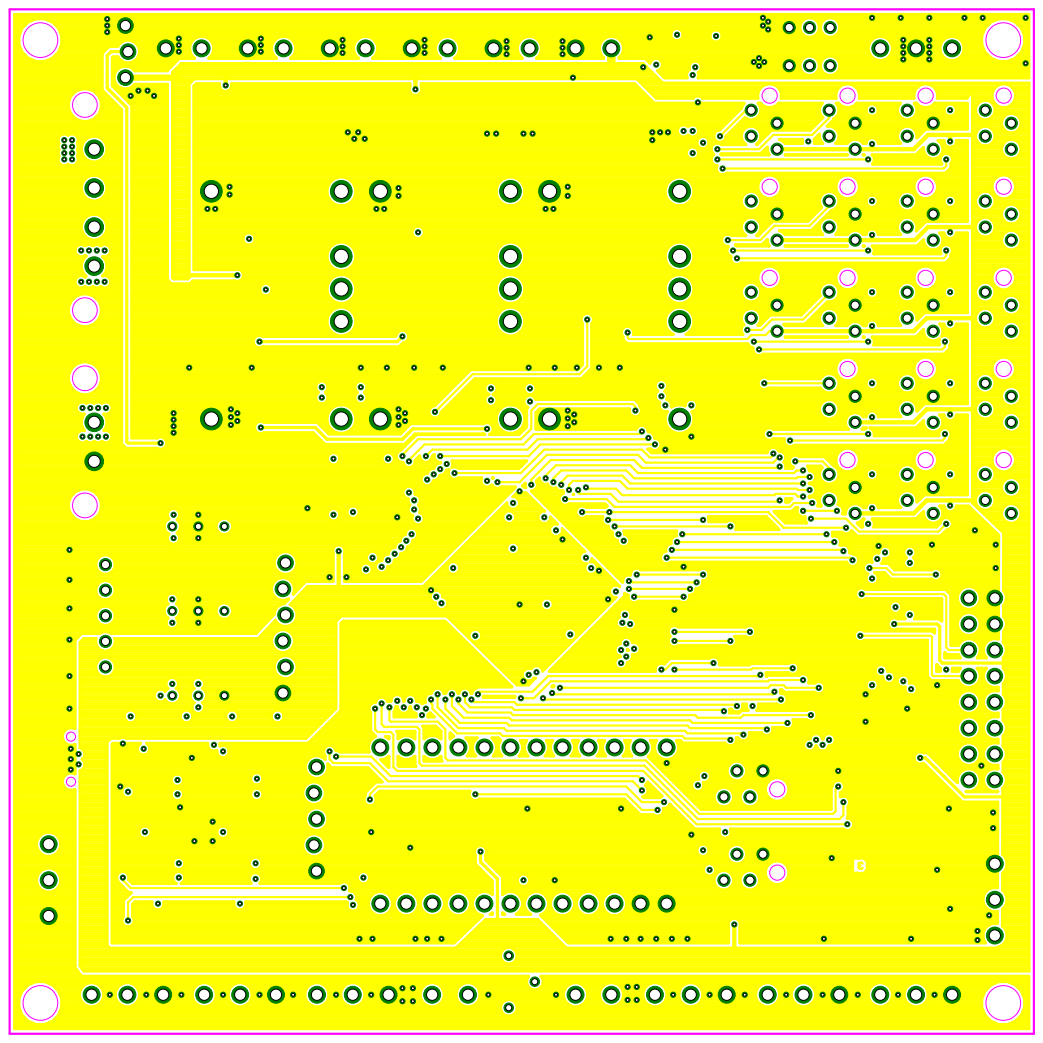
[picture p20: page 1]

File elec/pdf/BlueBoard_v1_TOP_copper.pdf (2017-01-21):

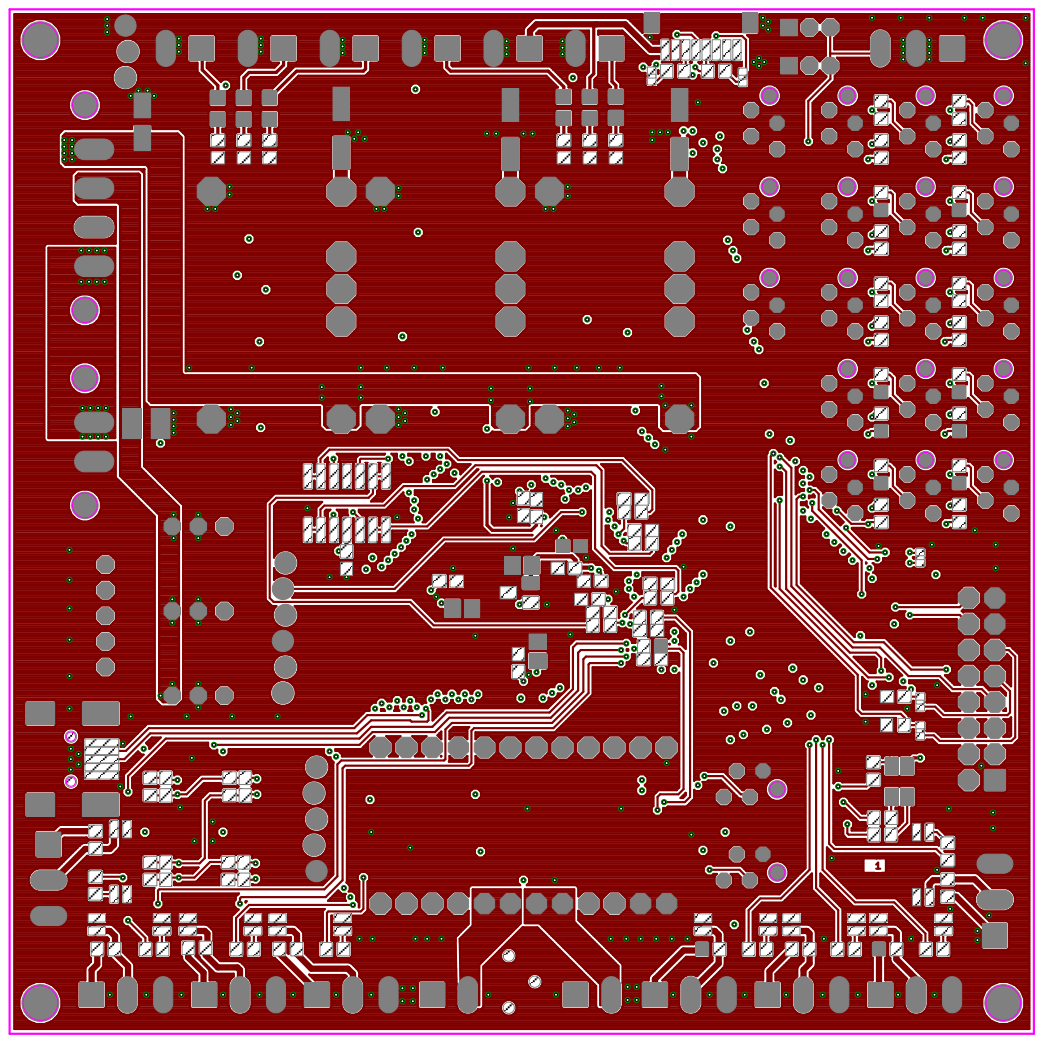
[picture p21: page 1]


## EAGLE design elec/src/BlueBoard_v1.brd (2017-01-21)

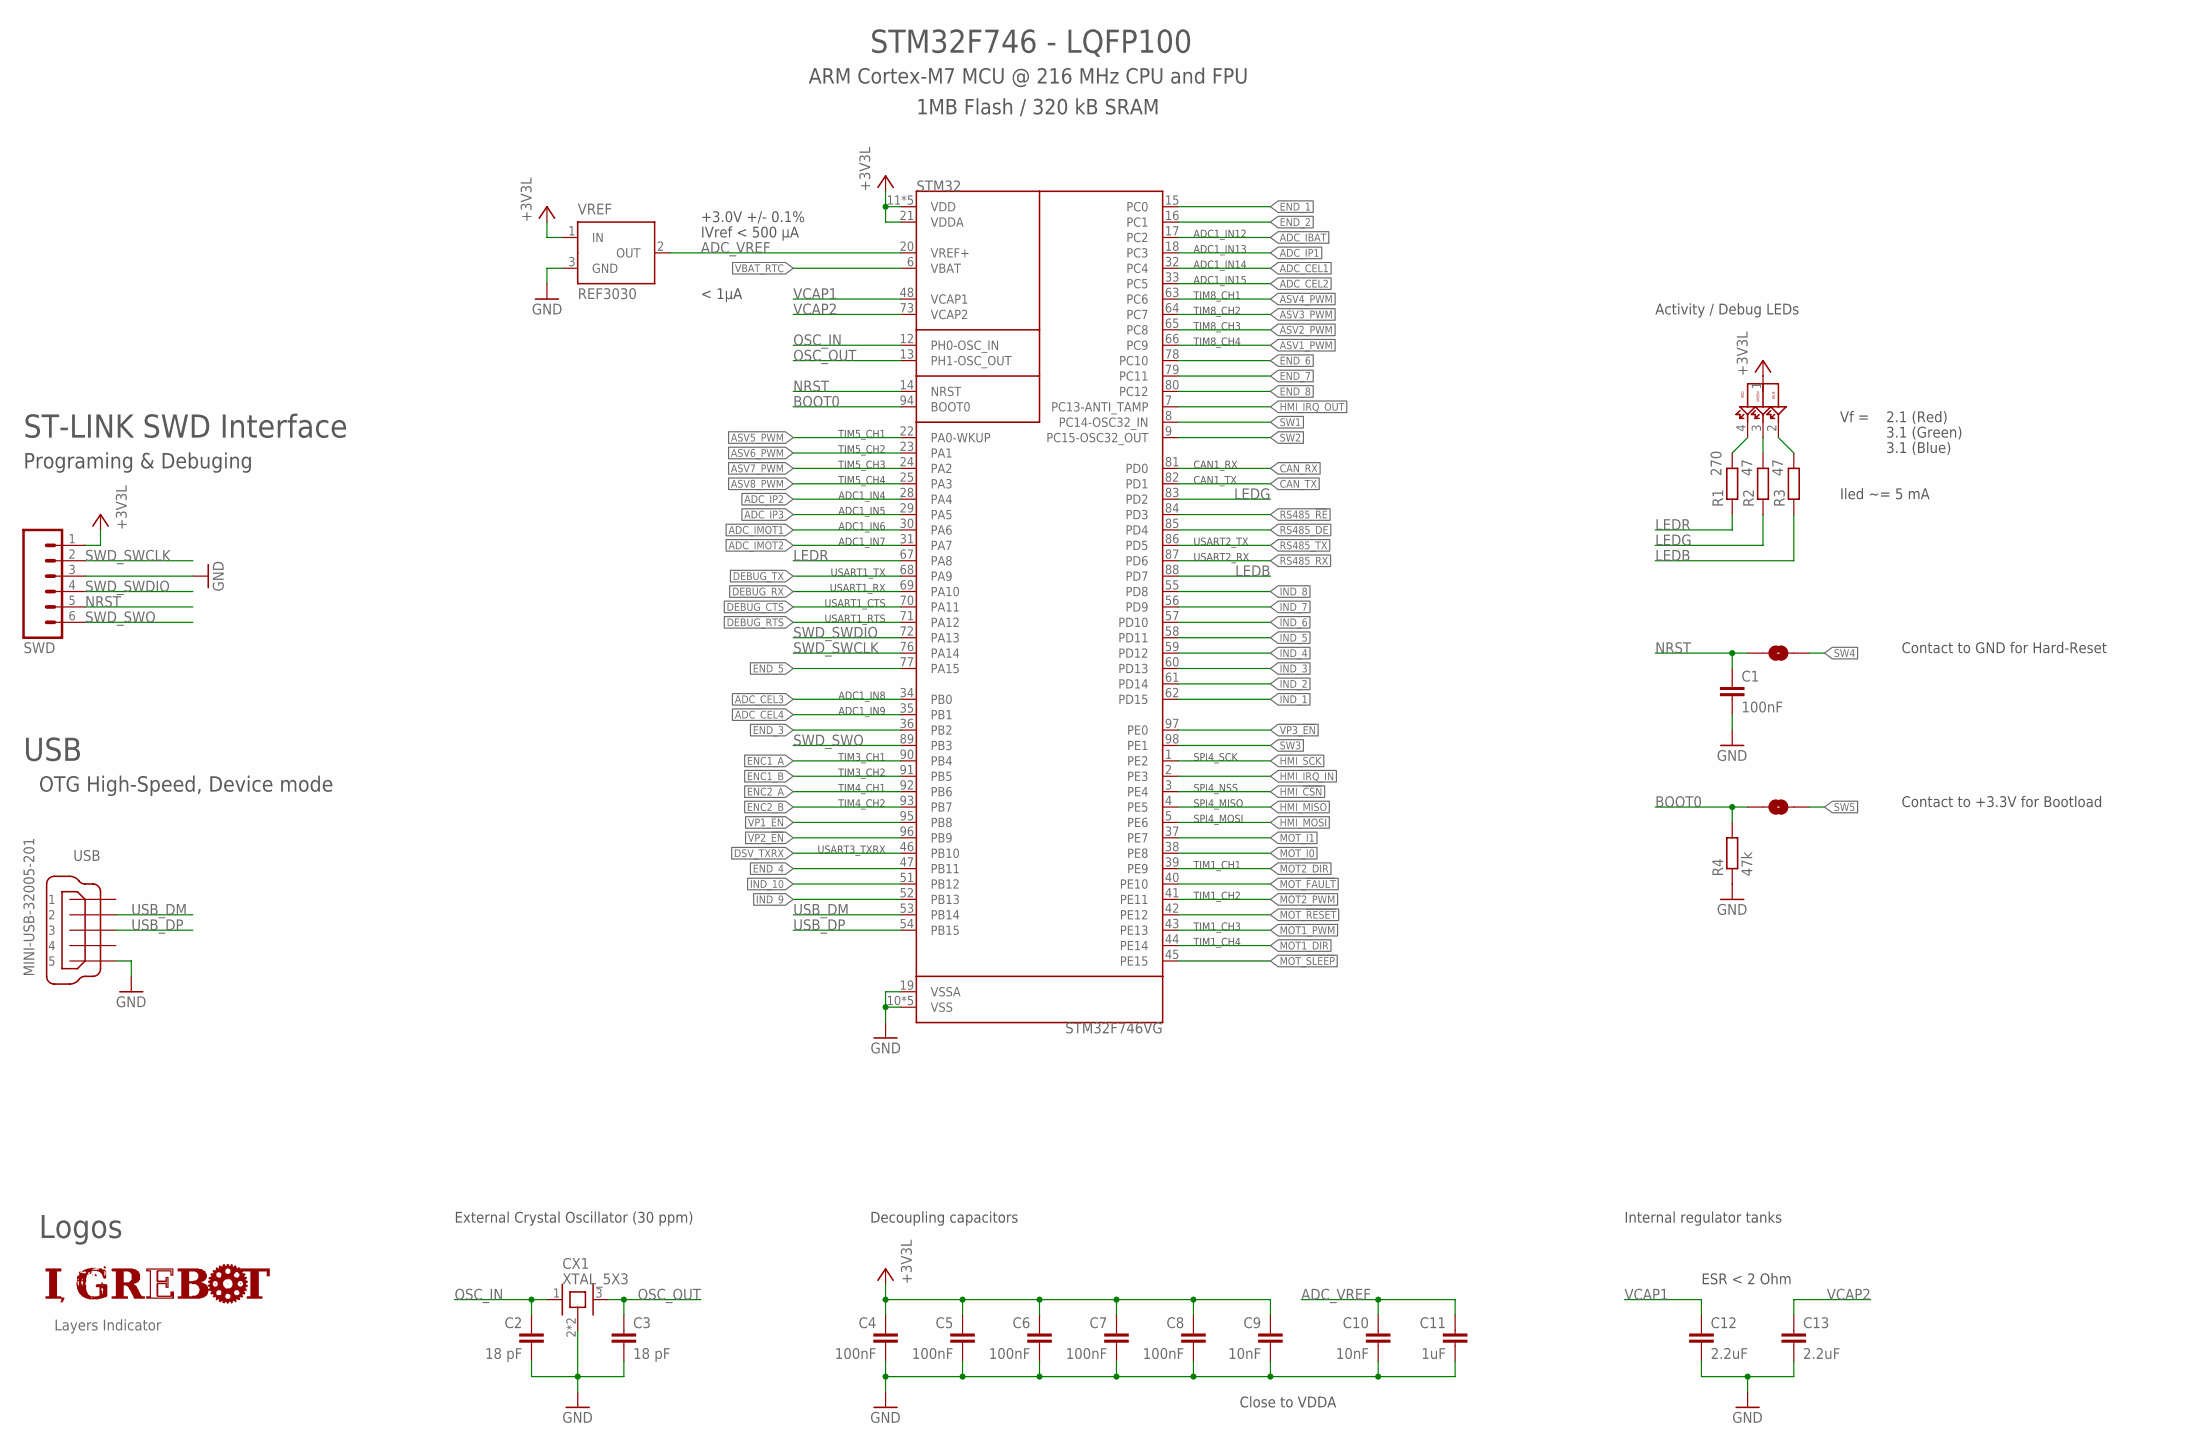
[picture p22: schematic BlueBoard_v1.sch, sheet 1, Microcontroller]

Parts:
C1, C4, C5, C6, C7, C8: 100nF; C0603
C2, C3: 18 pF; C0603
C9, C10: 10nF; C0603
C11: 1uF; C0805
C12, C13: 2.2uF; C0805
CX1: XTAL_5X3; CRYSTAL-OSC-SMD-5X3
LED1: ASMB-MTB0-0A3A2; PLCC4
LOGO_IGREBOT: LOGO_IGREBOT12X2MM; IGREBOT_12X2MM
LOGO_LAYERS: LAYERS_CHECK4_LAYERS; LAYERS_CHECK_4
R1: 270; R0603
R2, R3: 47; R0603
R4: 47k; R0603
SJ1, SJ2: SOLDERJUMPERNC2; SJ_2S-NOTRACE
STM32: STM32F746VG; LQFP_100
SWD: M06LOCK; 1X06_LOCK
USB: MINI-USB-32005-201; 32005-201
VREF: REF3030; SOT23

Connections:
+3V3L: C4.1, C5.1, C6.1, C7.1, C8.1, C9.1, LED1.1 (A), STM32.11 (VDD), STM32.21 (VDDA), STM32.27 (VDD), STM32.50 (VDD), STM32.75 (VDD), STM32.100 (VDD), SWD.1, VREF.1 (IN); also elsewhere on the board
ADC_CEL1: STM32.32 (PC4); also elsewhere on the board
ADC_CEL2: STM32.33 (PC5); also elsewhere on the board
ADC_CEL3: STM32.34 (PB0); also elsewhere on the board
ADC_CEL4: STM32.35 (PB1); also elsewhere on the board
ADC_IBAT: STM32.17 (PC2); also elsewhere on the board
ADC_IMOT1: STM32.30 (PA6); also elsewhere on the board
ADC_IMOT2: STM32.31 (PA7); also elsewhere on the board
ADC_IP1: STM32.18 (PC3); also elsewhere on the board
ADC_IP2: STM32.28 (PA4); also elsewhere on the board
ADC_IP3: STM32.29 (PA5); also elsewhere on the board
ADC_VREF: C10.1, C11.1, STM32.20 (VREF+), VREF.2 (OUT)
ASV1_PWM: STM32.66 (PC9); also elsewhere on the board
ASV2_PWM: STM32.65 (PC8); also elsewhere on the board
ASV3_PWM: STM32.64 (PC7); also elsewhere on the board
ASV4_PWM: STM32.63 (PC6); also elsewhere on the board
ASV5_PWM: STM32.22 (PA0-WKUP); also elsewhere on the board
ASV6_PWM: STM32.23 (PA1); also elsewhere on the board
ASV7_PWM: STM32.24 (PA2); also elsewhere on the board
ASV8_PWM: STM32.25 (PA3); also elsewhere on the board
BOOT0: R4.2, SJ2.1, STM32.94 (BOOT0)
CAN_RX: STM32.81 (PD0); also elsewhere on the board
CAN_TX: STM32.82 (PD1); also elsewhere on the board
DEBUG_CTS: STM32.70 (PA11); also elsewhere on the board
DEBUG_RTS: STM32.71 (PA12); also elsewhere on the board
DEBUG_RX: STM32.69 (PA10); also elsewhere on the board
DEBUG_TX: STM32.68 (PA9); also elsewhere on the board
DSV_TXRX: STM32.46 (PB10); also elsewhere on the board
ENC1_A: STM32.90 (PB4); also elsewhere on the board
ENC1_B: STM32.91 (PB5); also elsewhere on the board
ENC2_A: STM32.92 (PB6); also elsewhere on the board
ENC2_B: STM32.93 (PB7); also elsewhere on the board
END_1: STM32.15 (PC0); also elsewhere on the board
END_2: STM32.16 (PC1); also elsewhere on the board
END_3: STM32.36 (PB2); also elsewhere on the board
END_4: STM32.47 (PB11); also elsewhere on the board
END_5: STM32.77 (PA15); also elsewhere on the board
END_6: STM32.78 (PC10); also elsewhere on the board
END_7: STM32.79 (PC11); also elsewhere on the board
END_8: STM32.80 (PC12); also elsewhere on the board
GND: C1.2, C2.2, C3.2, C4.2, C5.2, C6.2, C7.2, C8.2, C9.2, C10.2, C11.2, C12.2, C13.2, CX1.2, CX1.4, R4.1, STM32.10 (VSS), STM32.19 (VSSA), STM32.26 (VSS), STM32.49 (VSS), STM32.74 (VSS), STM32.99 (VSS), SWD.3, USB.5, VREF.3 (GND); also elsewhere on the board
HMI_!CSN!: STM32.3 (PE4); also elsewhere on the board
HMI_IRQ_IN: STM32.2 (PE3); also elsewhere on the board
HMI_IRQ_OUT: STM32.7 (PC13-ANTI_TAMP); also elsewhere on the board
HMI_MISO: STM32.4 (PE5); also elsewhere on the board
HMI_MOSI: STM32.5 (PE6); also elsewhere on the board
HMI_SCK: STM32.1 (PE2); also elsewhere on the board
IND_1: STM32.62 (PD15); also elsewhere on the board
IND_2: STM32.61 (PD14); also elsewhere on the board
IND_3: STM32.60 (PD13); also elsewhere on the board
IND_4: STM32.59 (PD12); also elsewhere on the board
IND_5: STM32.58 (PD11); also elsewhere on the board
IND_6: STM32.57 (PD10); also elsewhere on the board
IND_7: STM32.56 (PD9); also elsewhere on the board
IND_8: STM32.55 (PD8); also elsewhere on the board
IND_9: STM32.52 (PB13); also elsewhere on the board
IND_10: STM32.51 (PB12); also elsewhere on the board
LEDB: R3.1, STM32.88 (PD7)
LEDG: R2.1, STM32.83 (PD2)
LEDR: R1.1, STM32.67 (PA8)
MOT1_DIR: STM32.44 (PE14); also elsewhere on the board
MOT1_PWM: STM32.43 (PE13); also elsewhere on the board
MOT2_DIR: STM32.39 (PE9); also elsewhere on the board
MOT2_PWM: STM32.41 (PE11); also elsewhere on the board
MOT_!FAULT!: STM32.40 (PE10); also elsewhere on the board
MOT_!RESET!: STM32.42 (PE12); also elsewhere on the board
MOT_!SLEEP!: STM32.45 (PE15); also elsewhere on the board
MOT_I0: STM32.38 (PE8); also elsewhere on the board
MOT_I1: STM32.37 (PE7); also elsewhere on the board
unnamed: LED1.4 (CR), R1.2
unnamed: LED1.3 (CG), R2.2
unnamed: LED1.2 (CB), R3.2
NRST: C1.1, SJ1.1, STM32.14 (NRST), SWD.5
OSC_IN: C2.1, CX1.1, STM32.12 (PH0-OSC_IN)
OSC_OUT: C3.1, CX1.3, STM32.13 (PH1-OSC_OUT)
RS485_!RE!: STM32.84 (PD3); also elsewhere on the board
RS485_DE: STM32.85 (PD4); also elsewhere on the board
RS485_RX: STM32.87 (PD6); also elsewhere on the board
RS485_TX: STM32.86 (PD5); also elsewhere on the board
SW1: STM32.8 (PC14-OSC32_IN); also elsewhere on the board
SW2: STM32.9 (PC15-OSC32_OUT); also elsewhere on the board
SW3: STM32.98 (PE1); also elsewhere on the board
SW4: SJ1.2; also elsewhere on the board
SW5: SJ2.2; also elsewhere on the board
SWD_SWCLK: STM32.76 (PA14), SWD.2
SWD_SWDIO: STM32.72 (PA13), SWD.4
SWD_SWO: STM32.89 (PB3), SWD.6
USB_DM: STM32.53 (PB14), USB.2
USB_DP: STM32.54 (PB15), USB.3
VBAT_RTC: STM32.6 (VBAT); also elsewhere on the board
VCAP1: C12.1, STM32.48 (VCAP1)
VCAP2: C13.1, STM32.73 (VCAP2)
VP1_!EN!: STM32.95 (PB8); also elsewhere on the board
VP2_!EN!: STM32.96 (PB9); also elsewhere on the board
VP3_!EN!: STM32.97 (PE0); also elsewhere on the board

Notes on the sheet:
Decoupling capacitors
ESR < 2 Ohm
< 1µA
TIM5_CH1
TIM5_CH2
TIM5_CH3
TIM5_CH4
USART1_TX
USART1_RX
USART1_CTS
USART1_RTS
TIM3_CH1
TIM3_CH2
TIM4_CH1
TIM4_CH2
USART3_TXRX
TIM1_CH4
TIM1_CH3
TIM1_CH2
TIM1_CH1
SPI4_MOSI
SPI4_MISO
SPI4_NSS
SPI4_SCK
USART2_RX
USART2_TX
CAN1_TX
CAN1_RX
TIM8_CH1
TIM8_CH2
TIM8_CH3
TIM8_CH4
USB
Programing & Debuging
ST-LINK SWD Interface
STM32F746 - LQFP100
ARM Cortex-M7 MCU @ 216 MHz CPU and FPU
1MB Flash / 320 kB SRAM
OTG High-Speed, Device mode
Internal regulator tanks

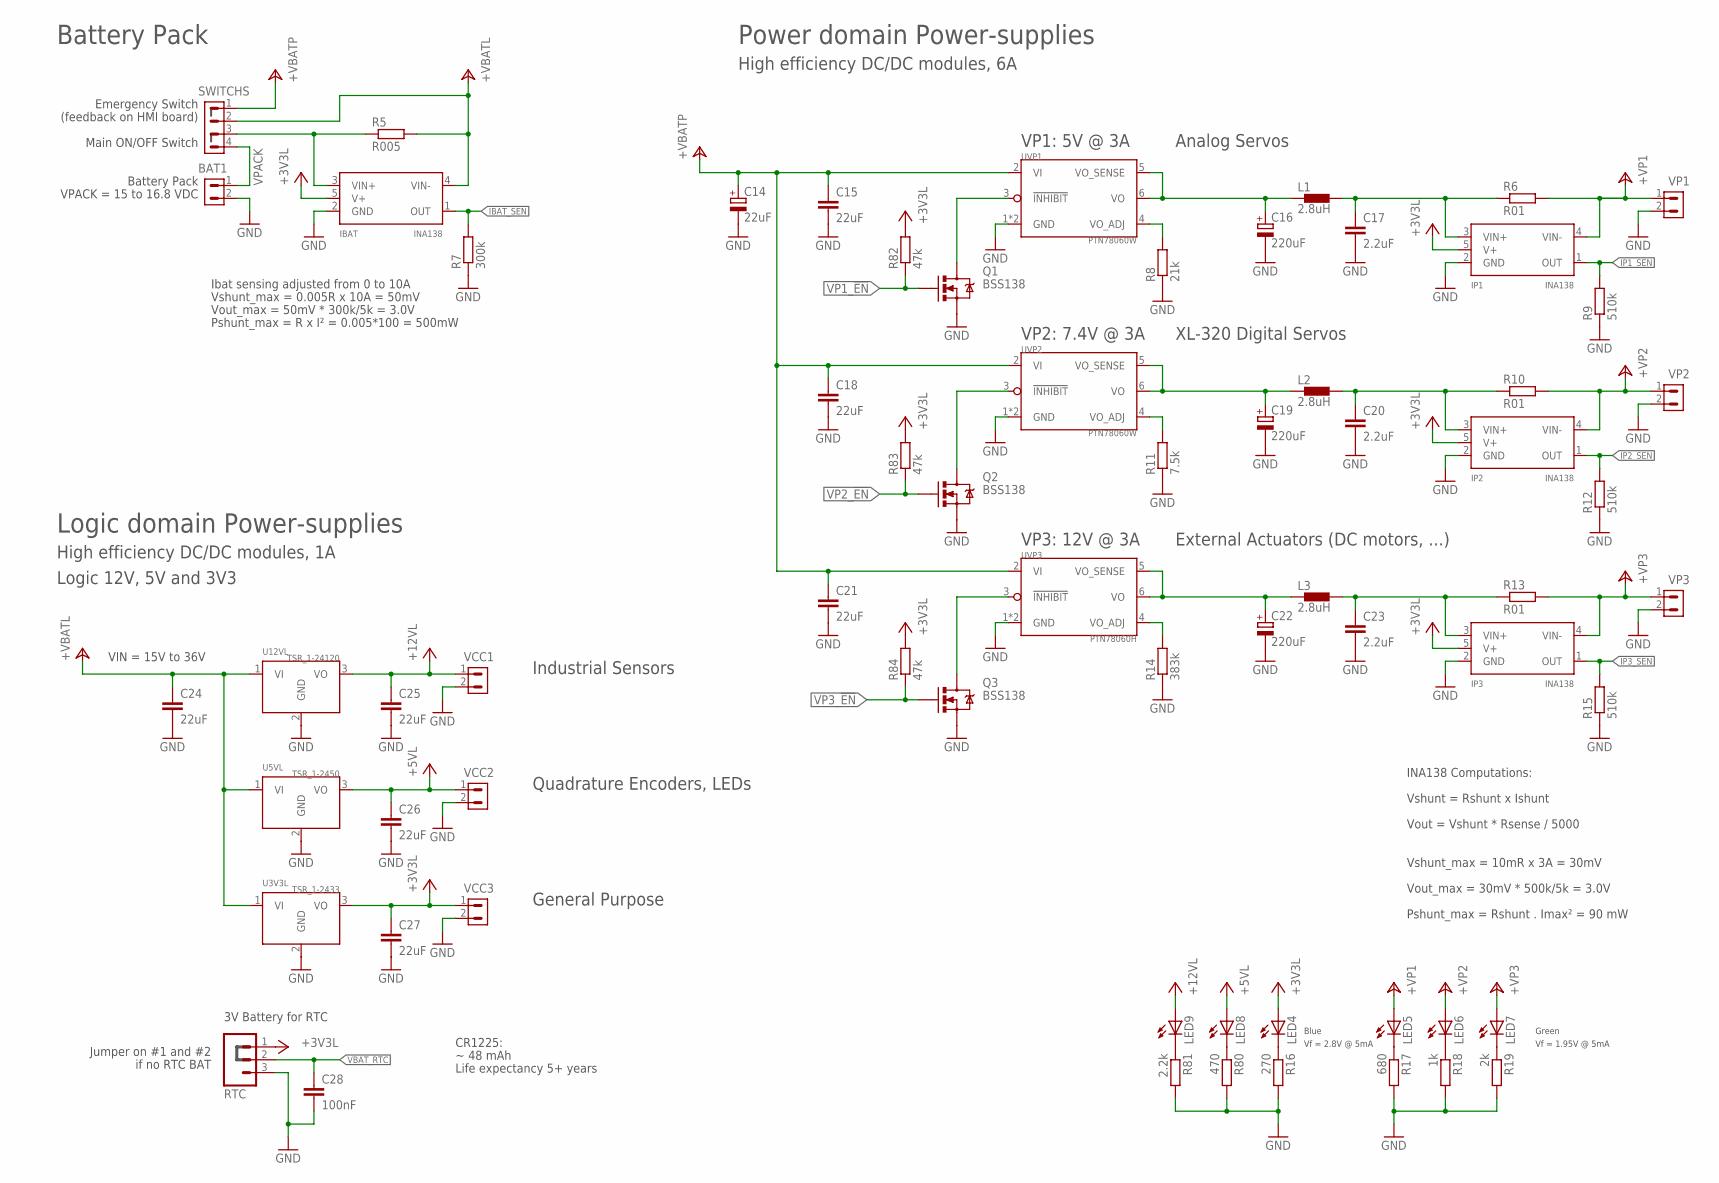
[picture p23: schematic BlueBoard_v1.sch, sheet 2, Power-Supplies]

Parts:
BAT1: MC15-GF-3.81-LR_2; CON_3.81_LR_2
C14: 22uF; PANASONIC_B
C15, C18, C21, C24: 22uF; C3225
C16, C19, C22: 220uF; PANASONIC_D
C17, C20, C23: 2.2uF; C3225
C25, C26, C27: 22uF; C1210
C28: 100nF; C0603
IBAT: INA138; DBV_05
IP1, IP2, IP3: INA138; DBV_05
L1, L2, L3: 2.8uH; DR1030
LED4, LED5, LED6, LED7, LED8, LED9: LEDCHIP-LED0805; CHIP-LED0805
Q1, Q2, Q3: BSS138; SOT23
R5: R005; R2512
R6, R10, R13: R01; R2512
R7: 300k; R0603
R8: 21k; R0603
R9, R12, R15: 510k; R0603
R11: 7.5k; R0603
R14: 383k; R0603
R16: 270; R0603
R17: 680; R0603
R18: 1k; R0603
R19: 2k; R0603
R80: 470; R0603
R81: 2.2k; R0603
R82, R83, R84: 47k; R0603
RTC: M03LOCK; 1X03_LOCK
SWITCHS: MC15-GF-3.81-LR_4; CON_3.81_LR_4
U3V3L: TSR_1-2433; TSR1
U5VL: TSR_1-2450; TSR1
U12VL: TSR_1-24120; TSR1
UVP1, UVP2: PTN78060W; PTN78060
UVP3: PTN78060H; PTN78060
VCC1, VCC2, VCC3: CON_3.5_2
VP1, VP2, VP3: CON_3.5_2

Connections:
!INHIBIT!_VP1: Q1.3 (D), UVP1.3 (!INHIBIT!)
!INHIBIT!_VP5: Q2.3 (D), UVP2.3 (!INHIBIT!)
!INHIBIT!_VP6: Q3.3 (D), UVP3.3 (!INHIBIT!)
+3V3L: C27.1, IBAT.5 (V+), IP1.5 (V+), IP2.5 (V+), IP3.5 (V+), LED4.A, R82.2, R83.2, R84.2, RTC.1, U3V3L.3 (VO), VCC3.1; also elsewhere on the board
+5VL: C26.1, LED8.A, U5VL.3 (VO), VCC2.1; also elsewhere on the board
+12VL: C25.1, LED9.A, U12VL.3 (VO), VCC1.1; also elsewhere on the board
+VBATL: C24.1, IBAT.4 (VIN-), R5.2, SWITCHS.2, U3V3L.1 (VI), U5VL.1 (VI), U12VL.1 (VI)
+VBATP: C14.+, C15.1, C18.1, C21.1, SWITCHS.1, UVP1.2 (VI), UVP2.2 (VI), UVP3.2 (VI); also elsewhere on the board
+VP1: IP1.4 (VIN-), LED5.A, R6.2, VP1.1; also elsewhere on the board
+VP2: IP2.4 (VIN-), LED6.A, R10.2, VP2.1; also elsewhere on the board
+VP3: IP3.4 (VIN-), LED7.A, R13.2, VP3.1
GND: BAT1.2, C14.-, C15.2, C16.-, C17.2, C18.2, C19.-, C20.2, C21.2, C22.-, C23.2, C24.2, C25.2, C26.2, C27.2, C28.2, IBAT.2 (GND), IP1.2 (GND), IP2.2 (GND), IP3.2 (GND), Q1.2 (S), Q2.2 (S), Q3.2 (S), R7.1, R8.1, R9.1, R11.1, R12.1, R14.1, R15.1, R16.2, R17.2, R18.2, R19.2, R80.2, R81.2, RTC.3, U3V3L.2 (GND), U5VL.2 (GND), U12VL.2 (GND), UVP1.1 (GND), UVP1.7 (GND), UVP2.1 (GND), UVP2.7 (GND), UVP3.1 (GND), UVP3.7 (GND), VCC1.2, VCC2.2, VCC3.2, VP1.2, VP2.2, VP3.2; also elsewhere on the board
IBAT_SEN: IBAT.1 (OUT), R7.2; also elsewhere on the board
IP1_SEN: IP1.1 (OUT), R9.2; also elsewhere on the board
IP2_SEN: IP2.1 (OUT), R12.2; also elsewhere on the board
IP3_SEN: IP3.1 (OUT), R15.2; also elsewhere on the board
unnamed: C16.+, L1.1, UVP1.5 (VO_SENSE), UVP1.6 (VO)
unnamed: C17.1, IP1.3 (VIN+), L1.2, R6.1
unnamed: R14.2, UVP3.4 (VO_ADJ)
unnamed: R11.2, UVP2.4 (VO_ADJ)
unnamed: C19.+, L2.1, UVP2.5 (VO_SENSE), UVP2.6 (VO)
unnamed: R8.2, UVP1.4 (VO_ADJ)
unnamed: C20.1, IP2.3 (VIN+), L2.2, R10.1
unnamed: C22.+, L3.1, UVP3.5 (VO_SENSE), UVP3.6 (VO)
unnamed: C23.1, IP3.3 (VIN+), L3.2, R13.1
unnamed: LED8.C, R80.1
unnamed: LED9.C, R81.1
unnamed: LED5.C, R17.1
unnamed: LED4.C, R16.1
unnamed: LED6.C, R18.1
unnamed: LED7.C, R19.1
unnamed: IBAT.3 (VIN+), R5.1, SWITCHS.3
VBAT_RTC: C28.1, RTC.2; also elsewhere on the board
VP1_!EN!: Q1.1 (G), R82.1; also elsewhere on the board
VP2_!EN!: Q2.1 (G), R83.1; also elsewhere on the board
VP3_!EN!: Q3.1 (G), R84.1; also elsewhere on the board
VPACK: BAT1.1, SWITCHS.4

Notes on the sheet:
VP1: 5V @ 3A
VP2: 7.4V @ 3A
Logic 12V, 5V and 3V3
VPACK = 15 to 16.8 VDC
Logic domain Power-supplies
High efficiency DC/DC modules, 1A
Power domain Power-supplies
High efficiency DC/DC modules, 6A
Battery Pack
Vshunt = Rshunt x Ishunt
Vout = Vshunt * Rsense / 5000
Vshunt_max = 10mR x 3A = 30mV
Vout_max = 30mV * 500k/5k = 3.0V
Emergency Switch
Main ON/OFF Switch
(feedback on HMI board)
Vshunt_max = 0.005R x 10A = 50mV
Vout_max = 50mV * 300k/5k = 3.0V
Ibat sensing adjusted from 0 to 10A
INA138 Computations:
Pshunt_max = R x I² = 0.005*100 = 500mW
Analog Servos
XL-320 Digital Servos
Industrial Sensors
General Purpose
Quadrature Encoders, LEDs
VP3: 12V @ 3A
External Actuators (DC motors, ...)
3V Battery for RTC
~ 48 mAh
Life expectancy 5+ years
Green
Blue
CR1225:
Pshunt_max = Rshunt . Imax² = 90 mW
Jumper on #1 and #2
if no RTC BAT
Vf = 2.8V @ 5mA
Vf = 1.95V @ 5mA
VIN = 15V to 36V

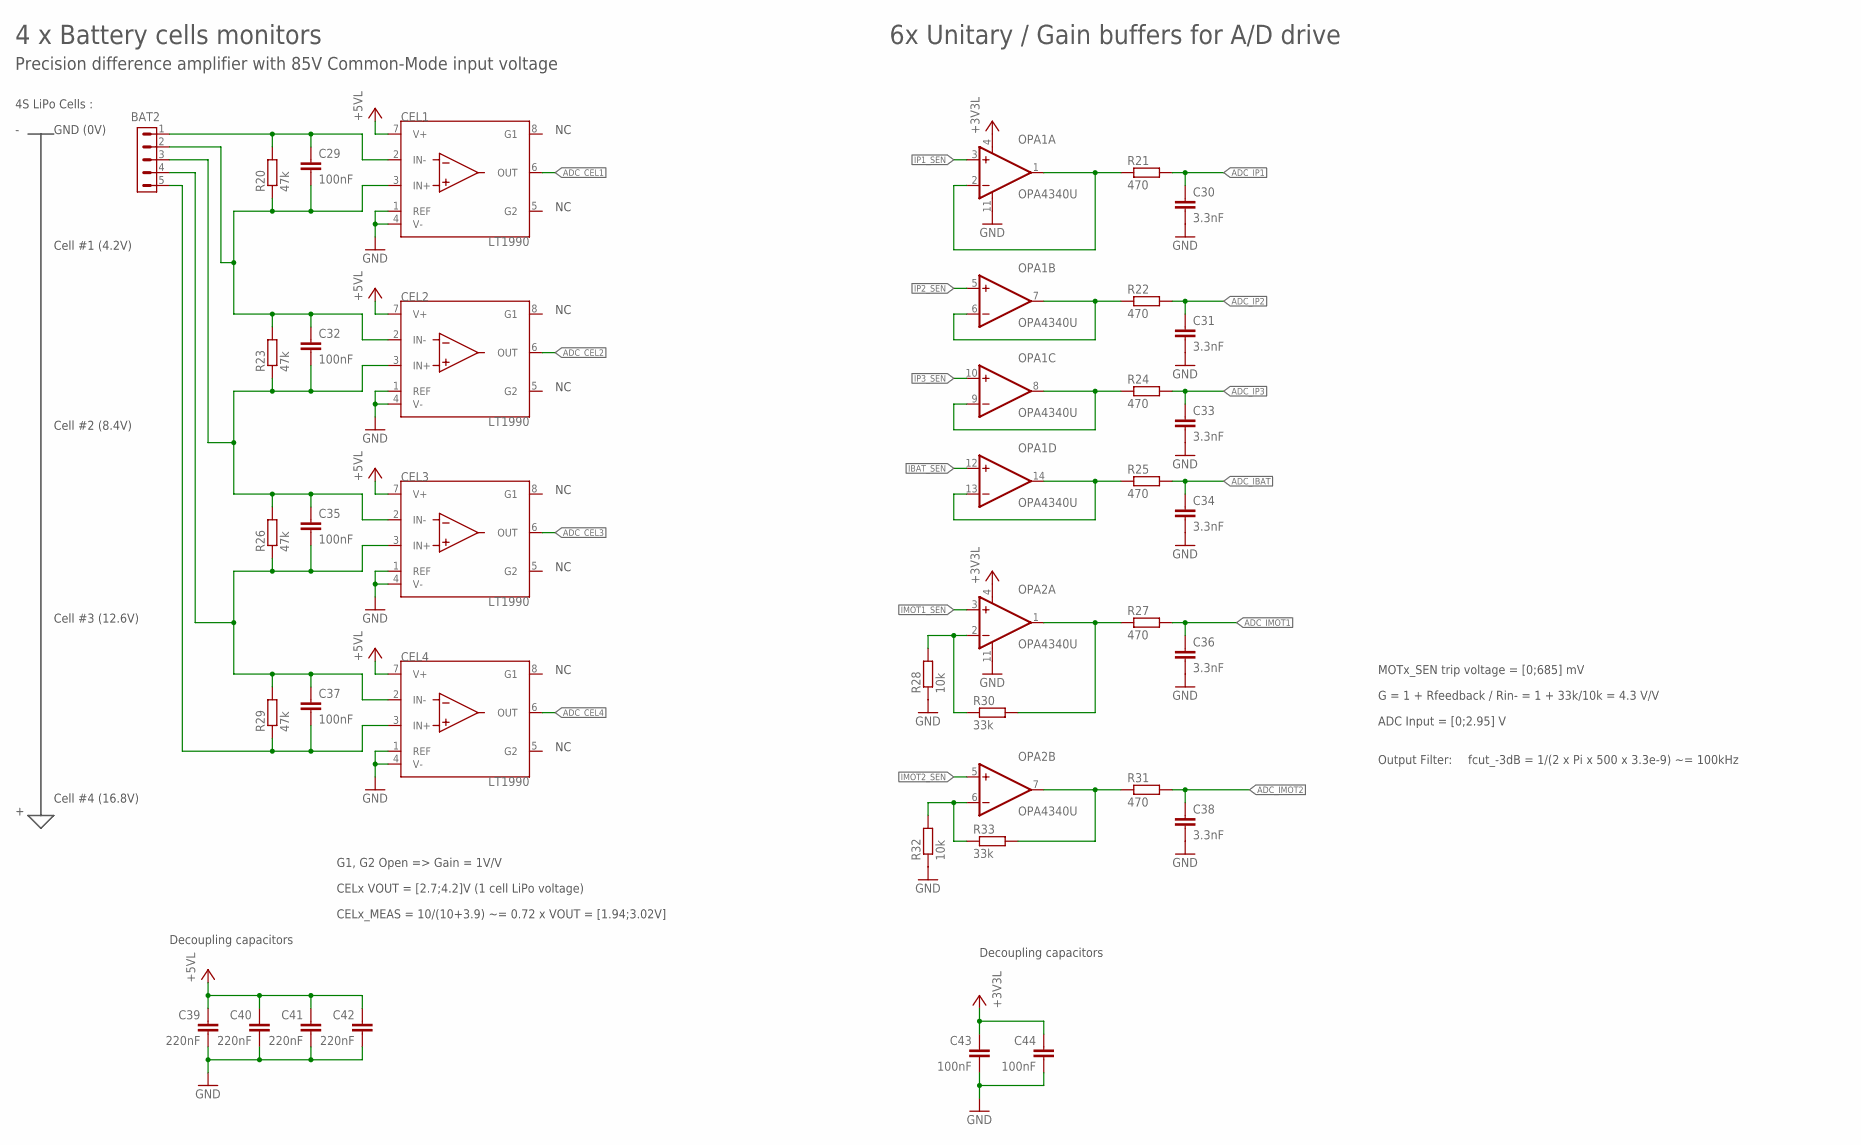
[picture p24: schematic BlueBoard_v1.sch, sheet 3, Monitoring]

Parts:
BAT2: JST-XH-S_5; JST-XH-5S
C29, C32, C35, C37, C43, C44: 100nF; C0603
C30, C31, C33, C34, C36, C38: 3.3nF; C0603
C39, C40, C41, C42: 220nF; C0603
CEL1, CEL2, CEL3, CEL4: LT1990; S8
OPA1, OPA2: OPA4340U; SO14
R20, R23, R26, R29: 47k; R0603
R21, R22, R24, R25, R27, R31: 470; R0603
R28, R32: 10k; R0603
R30, R33: 33k; R0603

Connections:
+3V3L: C43.1, C44.1, OPA1.4 (V+), OPA2.4 (V+); also elsewhere on the board
+5VL: C39.1, C40.1, C41.1, C42.1, CEL1.7 (V+), CEL2.7 (V+), CEL3.7 (V+), CEL4.7 (V+); also elsewhere on the board
ADC_CEL1: CEL1.6 (OUT); also elsewhere on the board
ADC_CEL2: CEL2.6 (OUT); also elsewhere on the board
ADC_CEL3: CEL3.6 (OUT); also elsewhere on the board
ADC_CEL4: CEL4.6 (OUT); also elsewhere on the board
ADC_IBAT: C34.1, R25.2; also elsewhere on the board
ADC_IMOT1: C36.1, R27.2; also elsewhere on the board
ADC_IMOT2: C38.1, R31.2; also elsewhere on the board
ADC_IP1: C30.1, R21.2; also elsewhere on the board
ADC_IP2: C31.1, R22.2; also elsewhere on the board
ADC_IP3: C33.1, R24.2; also elsewhere on the board
GND: C30.2, C31.2, C33.2, C34.2, C36.2, C38.2, C39.2, C40.2, C41.2, C42.2, C43.2, C44.2, CEL1.1 (REF), CEL1.4 (V-), CEL2.1 (REF), CEL2.4 (V-), CEL3.1 (REF), CEL3.4 (V-), CEL4.1 (REF), CEL4.4 (V-), OPA1.11 (V-), OPA2.11 (V-), R28.1, R32.1; also elsewhere on the board
IBAT_SEN: OPA1.12 (+IN); also elsewhere on the board
IMOT1_SEN: OPA2.3 (+IN); also elsewhere on the board
IMOT2_SEN: OPA2.5 (+IN); also elsewhere on the board
IP1_SEN: OPA1.3 (+IN); also elsewhere on the board
IP2_SEN: OPA1.5 (+IN); also elsewhere on the board
IP3_SEN: OPA1.10 (+IN); also elsewhere on the board
unnamed: OPA2.2 (-IN), R28.2, R30.1
unnamed: OPA2.6 (-IN), R32.2, R33.1
unnamed: OPA1.1 (OUT), OPA1.2 (-IN), R21.1
unnamed: OPA1.6 (-IN), OPA1.7 (OUT), R22.1
unnamed: OPA1.8 (OUT), OPA1.9 (-IN), R24.1
unnamed: OPA1.13 (-IN), OPA1.14 (OUT), R25.1
unnamed: OPA2.1 (OUT), R27.1, R30.2
unnamed: OPA2.7 (OUT), R31.1, R33.2
unnamed: BAT2.1, C29.1, CEL1.2 (IN-), R20.2
unnamed: BAT2.2, C29.2, C32.1, CEL1.3 (IN+), CEL2.2 (IN-), R20.1, R23.2
unnamed: BAT2.3, C32.2, C35.1, CEL2.3 (IN+), CEL3.2 (IN-), R23.1, R26.2
unnamed: BAT2.4, C35.2, C37.1, CEL3.3 (IN+), CEL4.2 (IN-), R26.1, R29.2
unnamed: BAT2.5, C37.2, CEL4.3 (IN+), R29.1

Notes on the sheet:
G1, G2 Open => Gain = 1V/V
CELx VOUT = [2.7;4.2]V (1 cell LiPo voltage)
CELx_MEAS = 10/(10+3.9) ~= 0.72 x VOUT = [1.94;3.02V]
4S LiPo Cells :
GND (0V)
Cell #1 (4.2V)
Cell #2 (8.4V)
Cell #3 (12.6V)
Cell #4 (16.8V)
4 x Battery cells monitors
Precision difference amplifier with 85V Common-Mode input voltage
fcut_-3dB = 1/(2 x Pi x 500 x 3.3e-9) ~= 100kHz
G = 1 + Rfeedback / Rin- = 1 + 33k/10k = 4.3 V/V
MOTx_SEN trip voltage = [0;685] mV
ADC Input = [0;2.95] V
6x Unitary / Gain buffers for A/D drive
Decoupling capacitors
Output Filter:

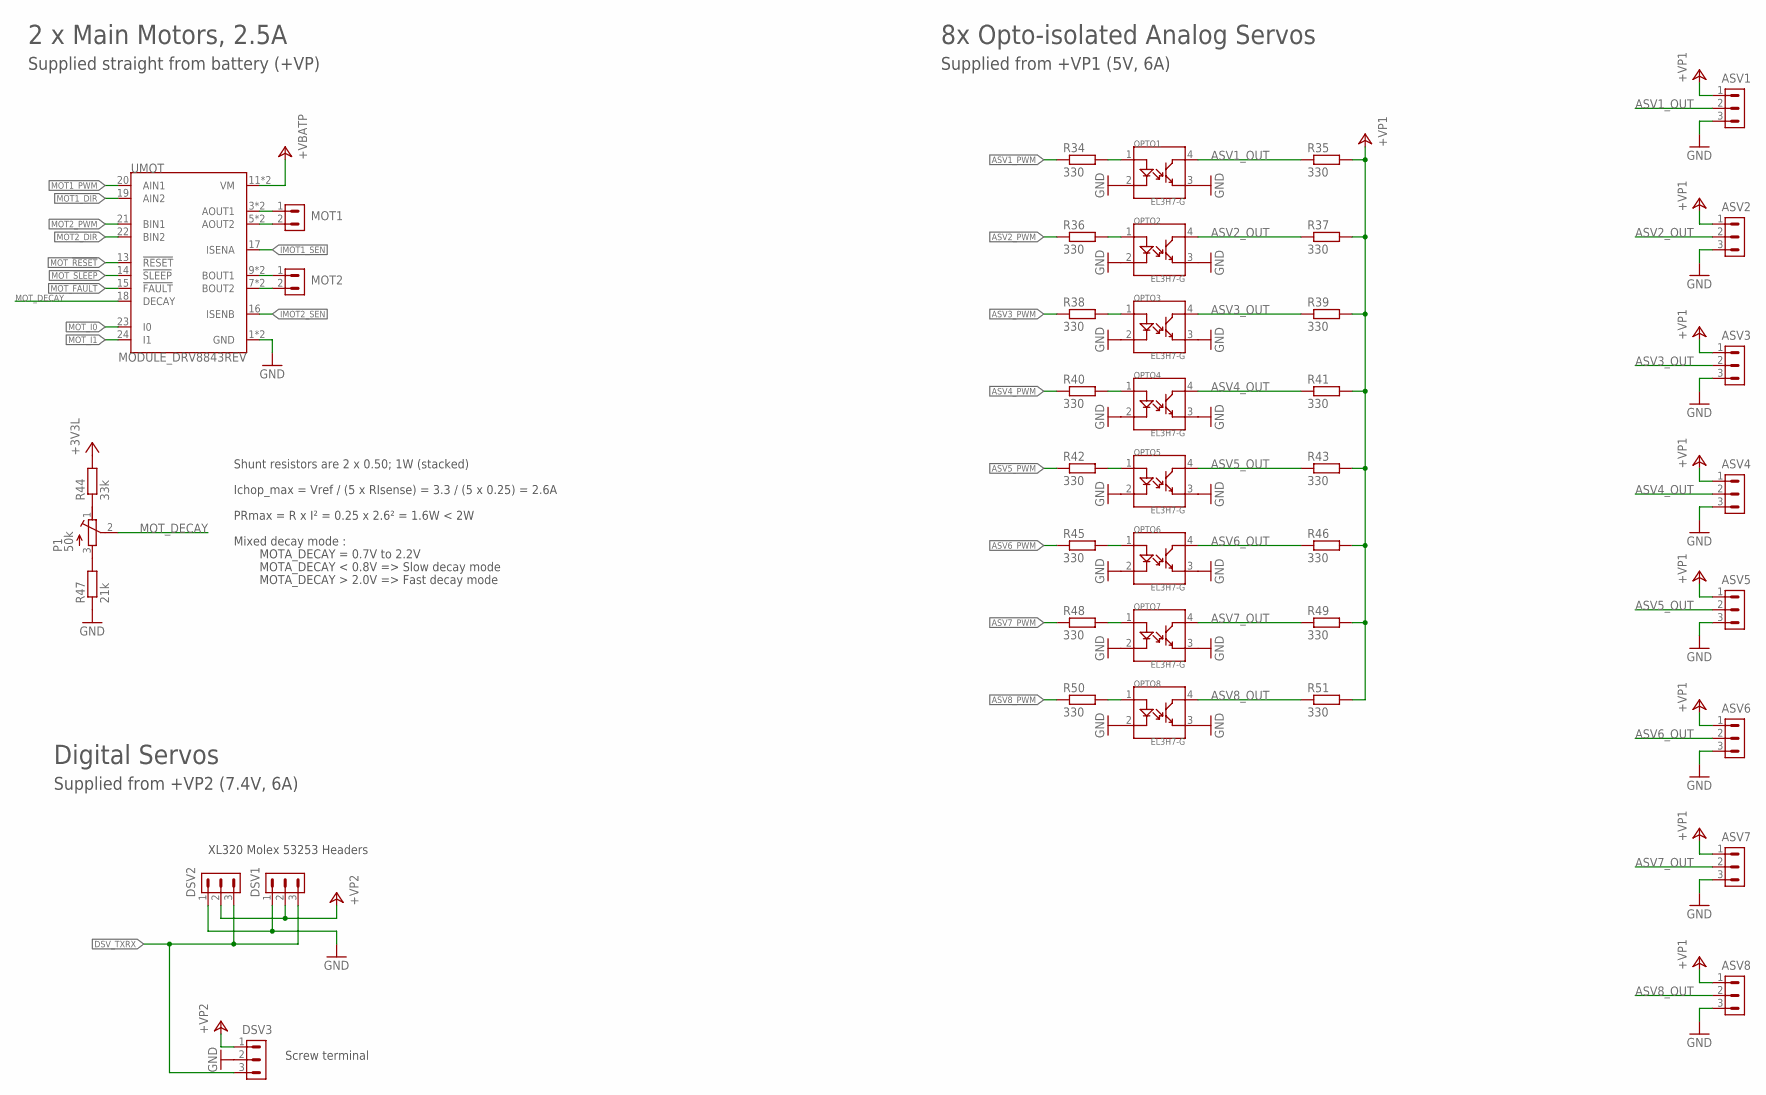
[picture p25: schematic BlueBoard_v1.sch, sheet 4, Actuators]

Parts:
ASV1, ASV2, ASV3, ASV4, ASV5, ASV6, ASV7, ASV8: CON_3.5_3
DSV1, DSV2: CON_2.00_MOLEX-53253_3
DSV3: CON_3.5_3
MOT1, MOT2: CON_3.5_2
OPTO1, OPTO2, OPTO3, OPTO4, OPTO5, OPTO6, OPTO7, OPTO8: EL3H7-G; SSOP_4
P1: 50k; RTRIMT93XB
R34, R35, R36, R37, R38, R39, R40, R41, R42, R43, R45, R46, R48, R49, R50, R51: 330; R0603
R44: 33k; R0603
R47: 21k; R0603
UMOT: MODULE_DRV8843REV; MODULE_DRV884X_REV

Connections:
+3V3L: R44.2; also elsewhere on the board
+VBATP: UMOT.11 (VM), UMOT.12 (VM); also elsewhere on the board
+VP1: ASV1.1, ASV2.1, ASV3.1, ASV4.1, ASV5.1, ASV6.1, ASV7.1, ASV8.1, R35.2, R37.2, R39.2, R41.2, R43.2, R46.2, R49.2, R51.2; also elsewhere on the board
+VP2: DSV1.2, DSV2.2, DSV3.1; also elsewhere on the board
ASV1_OUT: ASV1.2, OPTO1.4, R35.1
ASV1_PWM: R34.1; also elsewhere on the board
ASV2_OUT: ASV2.2, OPTO2.4, R37.1
ASV2_PWM: R36.1; also elsewhere on the board
ASV3_OUT: ASV3.2, OPTO3.4, R39.1
ASV3_PWM: R38.1; also elsewhere on the board
ASV4_OUT: ASV4.2, OPTO4.4, R41.1
ASV4_PWM: R40.1; also elsewhere on the board
ASV5_OUT: ASV5.2, OPTO5.4, R43.1
ASV5_PWM: R42.1; also elsewhere on the board
ASV6_OUT: ASV6.2, OPTO6.4, R46.1
ASV6_PWM: R45.1; also elsewhere on the board
ASV7_OUT: ASV7.2, OPTO7.4, R49.1
ASV7_PWM: R48.1; also elsewhere on the board
ASV8_OUT: ASV8.2, OPTO8.4, R51.1
ASV8_PWM: R50.1; also elsewhere on the board
DSV_TXRX: DSV1.3, DSV2.3, DSV3.3; also elsewhere on the board
GND: ASV1.3, ASV2.3, ASV3.3, ASV4.3, ASV5.3, ASV6.3, ASV7.3, ASV8.3, DSV1.1, DSV2.1, DSV3.2, OPTO1.2, OPTO1.3, OPTO2.2, OPTO2.3, OPTO3.2, OPTO3.3, OPTO4.2, OPTO4.3, OPTO5.2, OPTO5.3, OPTO6.2, OPTO6.3, OPTO7.2, OPTO7.3, OPTO8.2, OPTO8.3, R47.1, UMOT.1 (GND), UMOT.2 (GND); also elsewhere on the board
IMOT1_SEN: UMOT.17 (ISENA); also elsewhere on the board
IMOT2_SEN: UMOT.16 (ISENB); also elsewhere on the board
MOT1_DIR: UMOT.19 (AIN2); also elsewhere on the board
MOT1_PWM: UMOT.20 (AIN1); also elsewhere on the board
MOT2_DIR: UMOT.22 (BIN2); also elsewhere on the board
MOT2_PWM: UMOT.21 (BIN1); also elsewhere on the board
MOT_!FAULT!: UMOT.15 (!FAULT!); also elsewhere on the board
MOT_!RESET!: UMOT.13 (!RESET!); also elsewhere on the board
MOT_!SLEEP!: UMOT.14 (!SLEEP!); also elsewhere on the board
MOT_DECAY: P1.2 (S), UMOT.18 (DECAY)
MOT_I0: UMOT.23 (I0); also elsewhere on the board
MOT_I1: UMOT.24 (I1); also elsewhere on the board
unnamed: OPTO1.1, R34.2
unnamed: OPTO2.1, R36.2
unnamed: OPTO3.1, R38.2
unnamed: OPTO4.1, R40.2
unnamed: OPTO5.1, R42.2
unnamed: OPTO6.1, R45.2
unnamed: OPTO7.1, R48.2
unnamed: OPTO8.1, R50.2
unnamed: MOT1.1, UMOT.3 (AOUT1), UMOT.4 (AOUT1)
unnamed: MOT1.2, UMOT.5 (AOUT2), UMOT.6 (AOUT2)
unnamed: MOT2.1, UMOT.9 (BOUT1), UMOT.10 (BOUT1)
unnamed: MOT2.2, UMOT.7 (BOUT2), UMOT.8 (BOUT2)
unnamed: P1.3 (E), R47.2
unnamed: P1.1 (A), R44.1

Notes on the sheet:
2 x Main Motors, 2.5A
Ichop_max = Vref / (5 x RIsense) = 3.3 / (5 x 0.25) = 2.6A
PRmax = R x I² = 0.25 x 2.6² = 1.6W < 2W
Shunt resistors are 2 x 0.50; 1W (stacked)
Supplied straight from battery (+VP)
Mixed decay mode :
MOTA_DECAY = 0.7V to 2.2V
MOTA_DECAY < 0.8V => Slow decay mode
MOTA_DECAY > 2.0V => Fast decay mode
8x Opto-isolated Analog Servos
Supplied from +VP1 (5V, 6A)
Digital Servos
Supplied from +VP2 (7.4V, 6A)
Screw terminal
XL320 Molex 53253 Headers

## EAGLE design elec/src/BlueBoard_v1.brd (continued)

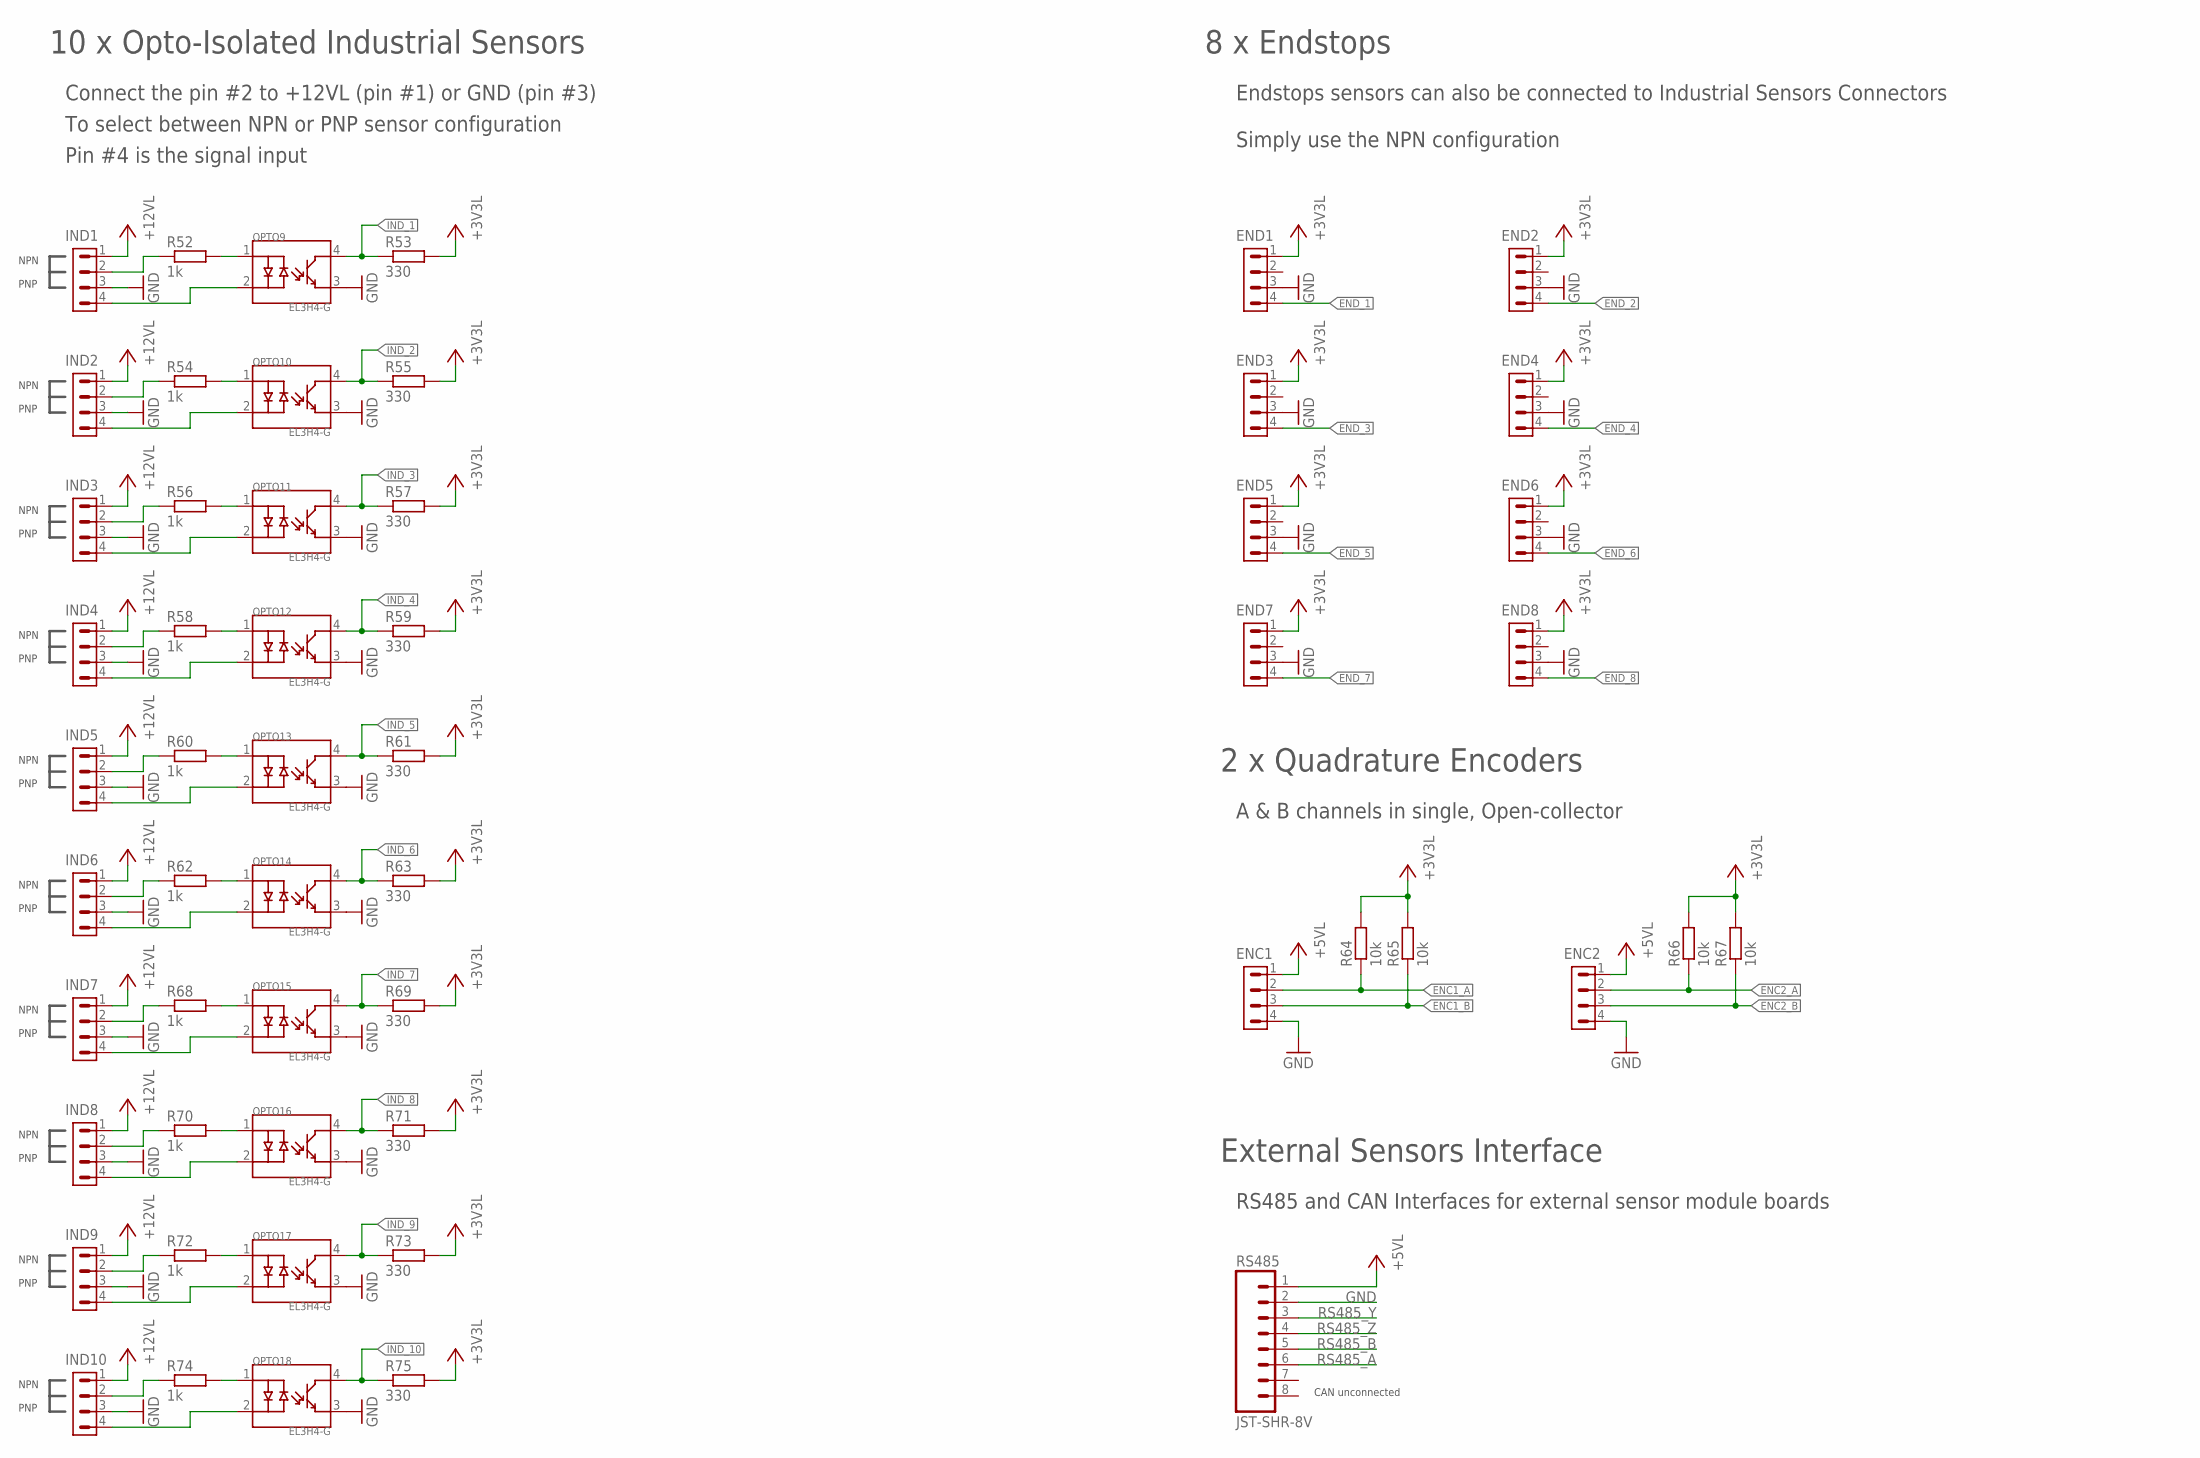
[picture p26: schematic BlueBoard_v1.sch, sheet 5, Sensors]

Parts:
ENC1, ENC2: CON_1.27_4
END1, END2, END3, END4, END5, END6, END7, END8: CON_1.27_4
IND1, IND2, IND3, IND4, IND5, IND6, IND7, IND8, IND9, IND10: CON_1.27_4
OPTO9, OPTO10, OPTO11, OPTO12, OPTO13, OPTO14, OPTO15, OPTO16, OPTO17, OPTO18: EL3H4-G; SSOP_4
R52, R54, R56, R58, R60, R62, R68, R70, R72, R74: 1k; R0603
R53, R55, R57, R59, R61, R63, R69, R71, R73, R75: 330; R0603
R64, R65, R66, R67: 10k; R0603
RS485: JST-SHR-8V; JST-SHR-08V

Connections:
+3V3L: END1.1, END2.1, END3.1, END4.1, END5.1, END6.1, END7.1, END8.1, R53.2, R55.2, R57.2, R59.2, R61.2, R63.2, R64.2, R65.2, R66.2, R67.2, R69.2, R71.2, R73.2, R75.2; also elsewhere on the board
+5VL: ENC1.1, ENC2.1, RS485.1; also elsewhere on the board
+12VL: IND1.1, IND2.1, IND3.1, IND4.1, IND5.1, IND6.1, IND7.1, IND8.1, IND9.1, IND10.1; also elsewhere on the board
ENC1_A: ENC1.2, R64.1; also elsewhere on the board
ENC1_B: ENC1.3, R65.1; also elsewhere on the board
ENC2_A: ENC2.2, R66.1; also elsewhere on the board
ENC2_B: ENC2.3, R67.1; also elsewhere on the board
END_1: END1.4; also elsewhere on the board
END_2: END2.4; also elsewhere on the board
END_3: END3.4; also elsewhere on the board
END_4: END4.4; also elsewhere on the board
END_5: END5.4; also elsewhere on the board
END_6: END6.4; also elsewhere on the board
END_7: END7.4; also elsewhere on the board
END_8: END8.4; also elsewhere on the board
GND: ENC1.4, ENC2.4, END1.3, END2.3, END3.3, END4.3, END5.3, END6.3, END7.3, END8.3, IND1.3, IND2.3, IND3.3, IND4.3, IND5.3, IND6.3, IND7.3, IND8.3, IND9.3, IND10.3, OPTO9.3, OPTO10.3, OPTO11.3, OPTO12.3, OPTO13.3, OPTO14.3, OPTO15.3, OPTO16.3, OPTO17.3, OPTO18.3, RS485.2; also elsewhere on the board
IND_1: OPTO9.4, R53.1; also elsewhere on the board
IND_2: OPTO10.4, R55.1; also elsewhere on the board
IND_3: OPTO11.4, R57.1; also elsewhere on the board
IND_4: OPTO12.4, R59.1; also elsewhere on the board
IND_5: OPTO13.4, R61.1; also elsewhere on the board
IND_6: OPTO14.4, R63.1; also elsewhere on the board
IND_7: OPTO15.4, R69.1; also elsewhere on the board
IND_8: OPTO16.4, R71.1; also elsewhere on the board
IND_9: OPTO17.4, R73.1; also elsewhere on the board
IND_10: OPTO18.4, R75.1; also elsewhere on the board
unnamed: IND1.2, R52.1
unnamed: OPTO9.1, R52.2
unnamed: IND1.4, OPTO9.2
unnamed: IND2.2, R54.1
unnamed: OPTO10.1, R54.2
unnamed: IND2.4, OPTO10.2
unnamed: IND3.2, R56.1
unnamed: OPTO11.1, R56.2
unnamed: IND3.4, OPTO11.2
unnamed: IND4.2, R58.1
unnamed: OPTO12.1, R58.2
unnamed: IND4.4, OPTO12.2
unnamed: IND5.2, R60.1
unnamed: OPTO13.1, R60.2
unnamed: IND5.4, OPTO13.2
unnamed: IND6.2, R62.1
unnamed: OPTO14.1, R62.2
unnamed: IND6.4, OPTO14.2
unnamed: IND7.2, R68.1
unnamed: OPTO15.1, R68.2
unnamed: IND7.4, OPTO15.2
unnamed: IND8.2, R70.1
unnamed: OPTO16.1, R70.2
unnamed: IND8.4, OPTO16.2
unnamed: IND9.2, R72.1
unnamed: OPTO17.1, R72.2
unnamed: IND9.4, OPTO17.2
unnamed: IND10.2, R74.1
unnamed: OPTO18.1, R74.2
unnamed: IND10.4, OPTO18.2
RS485_A: RS485.6; also elsewhere on the board
RS485_B: RS485.5; also elsewhere on the board
RS485_Y: RS485.3; also elsewhere on the board
RS485_Z: RS485.4; also elsewhere on the board

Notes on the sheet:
10 x Opto-Isolated Industrial Sensors
8 x Endstops
NPN
PNP
Connect the pin #2 to +12VL (pin #1) or GND (pin #3)
To select between NPN or PNP sensor configuration
Endstops sensors can also be connected to Industrial Sensors Connectors
Simply use the NPN configuration
External Sensors Interface
RS485 and CAN Interfaces for external sensor module boards
Pin #4 is the signal input
2 x Quadrature Encoders
A & B channels in single, Open-collector
CAN unconnected

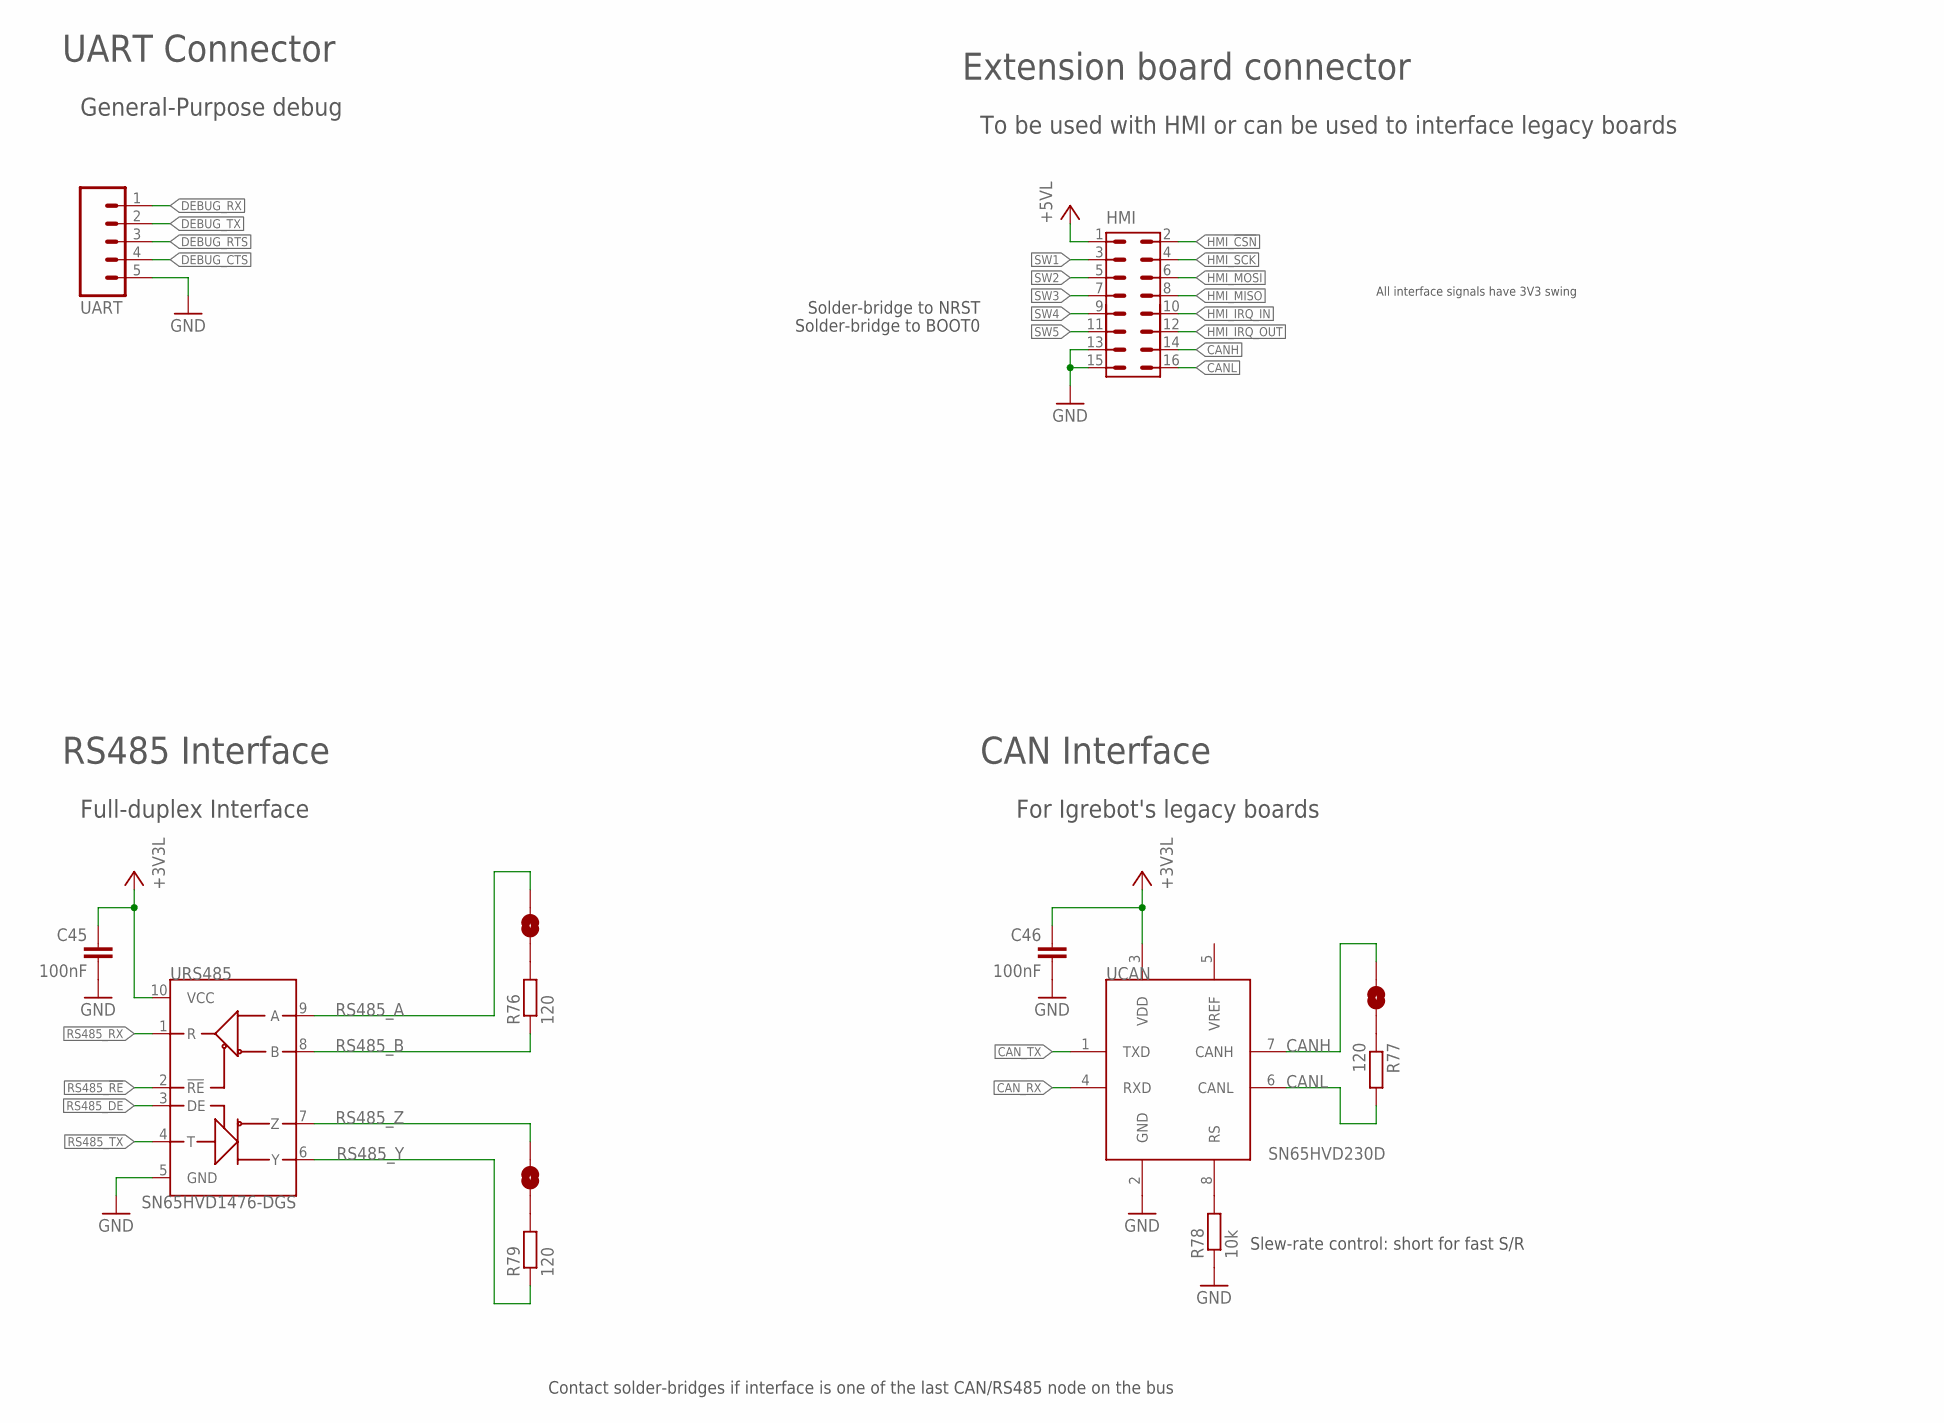
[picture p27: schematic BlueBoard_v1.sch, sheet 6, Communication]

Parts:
C45: 100nF; C0603K
C46: 100nF; C0603
HMI: HE10_V_16; CON_2X_2.54_V_16
R76, R77, R79: 120; R0603
R78: 10k; R0603
SJ3, SJ4, SJ5: SOLDERJUMPERNC2; SJ_2S-NOTRACE
UART: M05LOCK; 1X05_LOCK
UCAN: SN65HVD230D; SO-08
URS485: SN65HVD1476-DGS; MSOP-10

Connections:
+3V3L: C45.1, C46.1, UCAN.3 (VDD), URS485.10 (VCC); also elsewhere on the board
+5VL: HMI.1; also elsewhere on the board
CANH: HMI.14, SJ4.1, UCAN.7 (CANH)
CANL: HMI.16, R77.2, UCAN.6 (CANL)
CAN_RX: UCAN.4 (RXD); also elsewhere on the board
CAN_TX: UCAN.1 (TXD); also elsewhere on the board
DEBUG_CTS: UART.4; also elsewhere on the board
DEBUG_RTS: UART.3; also elsewhere on the board
DEBUG_RX: UART.1; also elsewhere on the board
DEBUG_TX: UART.2; also elsewhere on the board
GND: C45.2, C46.2, HMI.13, HMI.15, R78.1, UART.5, UCAN.2 (GND), URS485.5 (GND); also elsewhere on the board
HMI_!CSN!: HMI.2; also elsewhere on the board
HMI_IRQ_IN: HMI.10; also elsewhere on the board
HMI_IRQ_OUT: HMI.12; also elsewhere on the board
HMI_MISO: HMI.8; also elsewhere on the board
HMI_MOSI: HMI.6; also elsewhere on the board
HMI_SCK: HMI.4; also elsewhere on the board
unnamed: R78.2, UCAN.8 (RS)
unnamed: R77.1, SJ4.2
unnamed: R76.2, SJ3.2
unnamed: R79.2, SJ5.2
RS485_!RE!: URS485.2 (!RE!); also elsewhere on the board
RS485_A: SJ3.1, URS485.9 (A); also elsewhere on the board
RS485_B: R76.1, URS485.8 (B); also elsewhere on the board
RS485_DE: URS485.3 (DE); also elsewhere on the board
RS485_RX: URS485.1 (R); also elsewhere on the board
RS485_TX: URS485.4 (T); also elsewhere on the board
RS485_Y: R79.1, URS485.6 (Y); also elsewhere on the board
RS485_Z: SJ5.1, URS485.7 (Z); also elsewhere on the board
SW1: HMI.3; also elsewhere on the board
SW2: HMI.5; also elsewhere on the board
SW3: HMI.7; also elsewhere on the board
SW4: HMI.9; also elsewhere on the board
SW5: HMI.11; also elsewhere on the board

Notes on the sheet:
UART Connector
For Igrebot's legacy boards
CAN Interface
Contact solder-bridges if interface is one of the last CAN/RS485 node on the bus
RS485 Interface
Full-duplex Interface
To be used with HMI or can be used to interface legacy boards
Extension board connector
All interface signals have 3V3 swing
Solder-bridge to NRST
Solder-bridge to BOOT0
Slew-rate control: short for fast S/R
General-Purpose debug

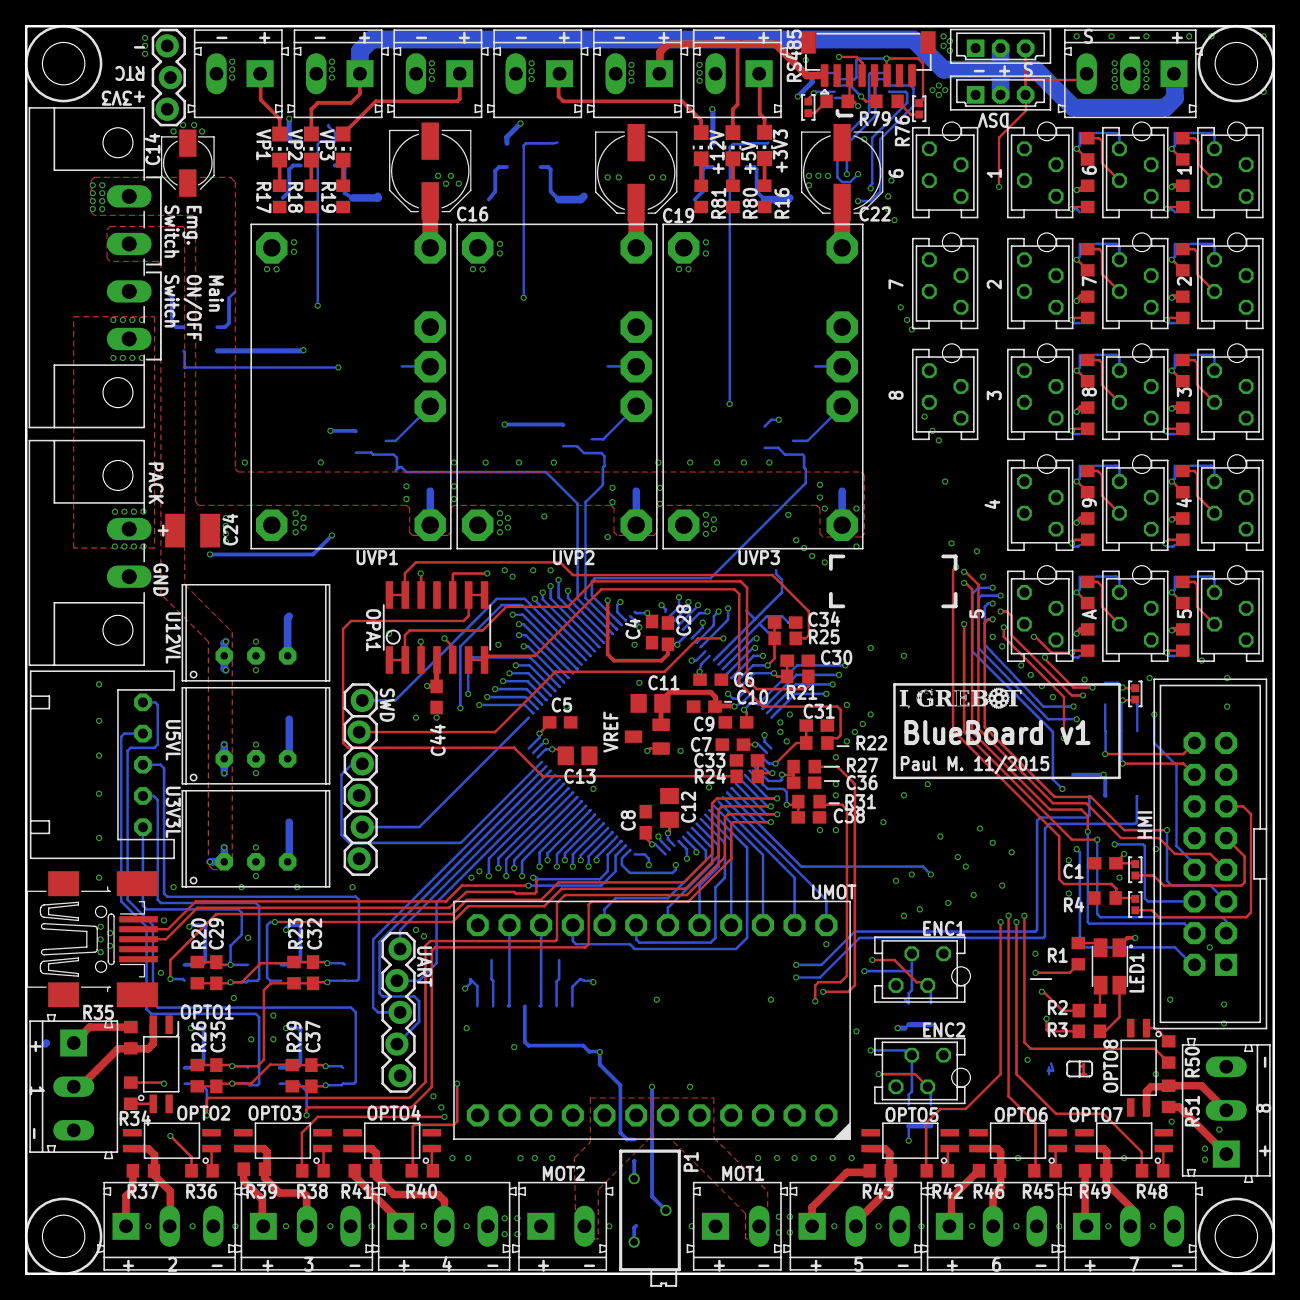
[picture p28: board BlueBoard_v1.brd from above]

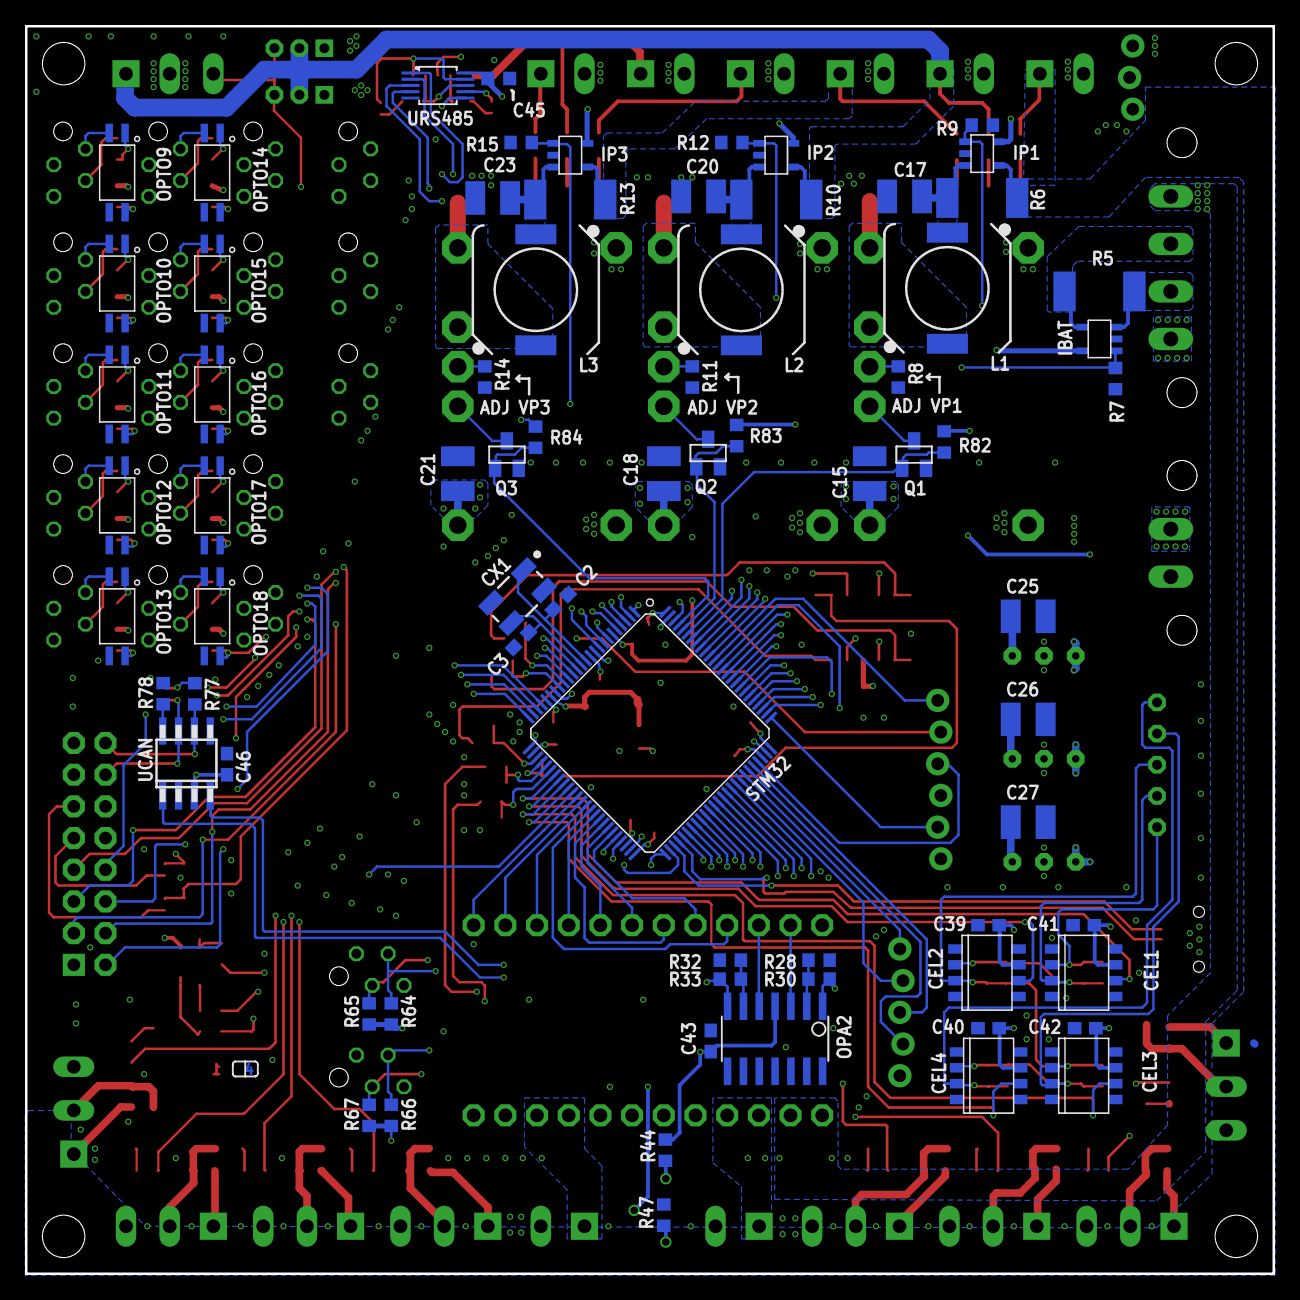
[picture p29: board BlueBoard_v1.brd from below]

Board: 4 copper layers, 100.0 x 100.0 mm, 239 parts (73 on the bottom side), 204 nets.

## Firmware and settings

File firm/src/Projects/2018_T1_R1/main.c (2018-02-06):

/* -----------------------------------------------------------------------------
 * BlueBoard
 * I-Grebot 2018
 * -----------------------------------------------------------------------------
 * @file       main.c
 * @author     Pierrick
 * @date       Jan 20, 2017
 * @version    V1.1
 * -----------------------------------------------------------------------------
 * @brief
 *   Main module of IgreBot's 2018 Robot #1 Firmware
 * -----------------------------------------------------------------------------
 * Versionning informations
 * Repository: https://github.com/I-Grebot/blueboard.git
 * -----------------------------------------------------------------------------
 */

/* General Header */
#include "../2018_T1_R1/include/main.h"

/**
********************************************************************************
**
**  Main Program
**
********************************************************************************
*/

int main( void )
{
  // BlueBoard Initialization
  bb_init();

  // Serial and shell are started first, so that errors can be displayed
  serial_init();

  if(shell_start() != pdPASS)
  {
    LEDR_WRITE(LEDx_ON); // Indicate error
    while(true);
  }

  // Main sequencer start
  sequencer_start();

  // Start FreeRTOS Scheduler
  vTaskStartScheduler();

  // Infinite loop
  while(true);

  // Should never reach this line!
  return 0;
}

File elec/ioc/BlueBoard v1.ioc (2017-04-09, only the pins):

Mcu.UserName=STM32F746VGTx
PA0/WKUP.GPIO_Label=ASV5_PWM
PA0/WKUP.Signal=S_TIM5_CH1
PA1.GPIO_Label=ASV6_PWM
PA1.Signal=S_TIM5_CH2
PA10.GPIO_Label=DEBUG_RX
PA10.Signal=USART1_RX
PA11.GPIO_Label=DEBUG_CTS
PA11.Signal=USART1_CTS
PA12.GPIO_Label=DEBUG_RTS
PA12.Signal=USART1_RTS
PA13.Signal=SYS_JTMS-SWDIO
PA14.Signal=SYS_JTCK-SWCLK
PA15.GPIO_Label=END_5
PA15.Signal=GPIO_Input
PA2.GPIO_Label=ASV7_PWM
PA2.Signal=S_TIM5_CH3
PA3.GPIO_Label=ASV8_PWM
PA3.Signal=S_TIM5_CH4
PA4.GPIO_Label=ADC_IP2
PA4.Signal=ADCx_IN4
PA5.GPIO_Label=ADC_IP3
PA5.Signal=ADCx_IN5
PA6.GPIO_Label=ADC_IMOT1
PA6.Signal=ADCx_IN6
PA7.GPIO_Label=ADC_IMOT2
PA7.Signal=ADCx_IN7
PA8.GPIO_Label=LEDR
PA8.Signal=GPIO_Output
PA9.GPIO_Label=DEBUG_TX
PA9.Signal=USART1_TX
PB0.GPIO_Label=ADC_CEL3
PB0.Signal=ADCx_IN8
PB1.GPIO_Label=ADC_CEL4
PB1.Signal=ADCx_IN9
PB10.GPIO_Label=DSV_TXRX
PB10.Signal=USART3_TX
PB11.GPIO_Label=END_4
PB11.Signal=GPIO_Input
PB12.GPIO_Label=IND_10
PB12.Signal=GPIO_Input
PB13.GPIO_Label=IND_9
PB13.Signal=GPIO_Input
PB14.Signal=USB_OTG_HS_DM
PB15.Signal=USB_OTG_HS_DP
PB2.GPIO_Label=END_3
PB2.Signal=GPIO_Input
PB3.Signal=SYS_JTDO-SWO
PB4.GPIO_Label=ENC1_A
PB4.Signal=S_TIM3_CH1
PB5.GPIO_Label=ENC1_B
PB5.Signal=S_TIM3_CH2
PB6.GPIO_Label=ENC2_A
PB6.Signal=S_TIM4_CH1
PB7.GPIO_Label=ENC2_B
PB7.Signal=S_TIM4_CH2
PB8.GPIO_Label=VP1_nEN
PB8.Signal=GPIO_Output
PB9.GPIO_Label=VP2_nEN
PB9.Signal=GPIO_Output
PC0.GPIO_Label=END_1
PC0.Signal=GPIO_Input
PC1.GPIO_Label=END_2
PC1.Signal=GPIO_Input
PC10.GPIO_Label=END_6
PC10.Signal=GPIO_Input
PC11.GPIO_Label=END_7
PC11.Signal=GPIO_Input
PC12.GPIO_Label=END_8
PC12.Signal=GPIO_Input
PC13.GPIO_Label=HMI_IRQ_OUT
PC13.Signal=GPIO_Output
PC14/OSC32_IN.GPIO_Label=SW1
PC14/OSC32_IN.Signal=GPIO_Input
PC15/OSC32_OUT.GPIO_Label=SW2
PC15/OSC32_OUT.Signal=GPIO_Input
PC2.GPIO_Label=ADC_IBAT
PC2.Signal=ADCx_IN12
PC3.GPIO_Label=ADC_IP1
PC3.Signal=ADCx_IN13
PC4.GPIO_Label=ADC_CEL1
PC4.Signal=ADCx_IN14
PC5.GPIO_Label=ADC_CEL2
PC5.Signal=ADCx_IN15
PC6.GPIO_Label=ASV4_PWM
PC6.Signal=S_TIM8_CH1
PC7.GPIO_Label=ASV3_PWM
PC7.Signal=S_TIM8_CH2
PC8.GPIO_Label=ASV2_PWM
PC8.Signal=S_TIM8_CH3
PC9.GPIO_Label=ASV1_PWM
PC9.Signal=S_TIM8_CH4
PD0.Signal=CAN1_RX
PD1.Signal=CAN1_TX
PD10.GPIO_Label=IND_6
PD10.Signal=GPIO_Input
PD11.GPIO_Label=IND_5
PD11.Signal=GPIO_Input
PD12.GPIO_Label=IND_4
PD12.Signal=GPIO_Input
PD13.GPIO_Label=IND_3
PD13.Signal=GPIO_Input
PD14.GPIO_Label=IND_2
PD14.Signal=GPIO_Input
PD15.GPIO_Label=IND_1
PD15.Signal=GPIO_Input
PD2.GPIO_Label=LEDG
PD2.Signal=GPIO_Output
PD3.GPIO_Label=RS485_nRE
PD3.Signal=GPIO_Output
PD4.GPIO_Label=RS485_DE
PD4.Signal=GPIO_Output
PD5.GPIO_Label=RS485_TX
PD5.Signal=USART2_TX
PD6.GPIO_Label=RS485_RX
PD6.Signal=USART2_RX
PD7.GPIO_Label=LEDB
PD7.Signal=GPIO_Output
PD8.GPIO_Label=IND_8
PD8.Signal=GPIO_Input
PD9.GPIO_Label=IND_7
PD9.Signal=GPIO_Input
PE0.GPIO_Label=VP3_nEN
PE0.Signal=GPIO_Output
PE1.GPIO_Label=SW3
PE1.Signal=GPIO_Input
PE10.GPIO_Label=MOT_nFAULT
PE10.Signal=GPIO_Input
PE11.GPIO_Label=MOT2_PWM
PE11.Signal=S_TIM1_CH2
PE12.GPIO_Label=MOT_nRESET
PE12.Signal=GPIO_Output
PE13.GPIO_Label=MOT1_PWM
PE13.Signal=S_TIM1_CH3
PE14.GPIO_Label=MOT1_DIR
PE14.Signal=S_TIM1_CH4
PE15.GPIO_Label=MOT_nSLEEP
PE15.Signal=GPIO_Output
PE2.GPIO_Label=HMI_SCK
PE2.Signal=SPI4_SCK
PE3.GPIO_Label=HMI_IRQ_IN
PE3.Signal=GPIO_Input
PE4.Signal=SPI4_NSS
PE5.GPIO_Label=HMI_MISO
PE5.Signal=SPI4_MISO
PE6.GPIO_Label=HMI_MOSI
PE6.Signal=SPI4_MOSI
PE7.GPIO_Label=MOT_I1
PE7.Signal=GPIO_Output
PE8.GPIO_Label=MOT_I0
PE8.Signal=GPIO_Output
PE9.GPIO_Label=MOT2_DIR
PE9.Signal=S_TIM1_CH1
PH0/OSC_IN.Signal=RCC_OSC_IN
PH1/OSC_OUT.Signal=RCC_OSC_OUT

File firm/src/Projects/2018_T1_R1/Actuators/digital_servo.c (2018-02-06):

/* -----------------------------------------------------------------------------
 * BlueBoard
 * I-Grebot
 * -----------------------------------------------------------------------------
 * @file       digital_servo.c
 * @author     Pierrick
 * @date       Apr 27, 2016
 * @version    V1.0
 * -----------------------------------------------------------------------------
 * @brief
 *   This module handles the digital servos
 * -----------------------------------------------------------------------------
 * Versionning informations
 * Repository: https://github.com/I-Grebot/blueboard.git
 * -----------------------------------------------------------------------------
 */

/* Inclusion */
#include "../../2018_T1_R1/include/main.h"

/* UART Configuration handlers */
//USART_InitTypeDef dsv_itf1_uart;
//USART_InitTypeDef dsv_itf2_uart;

/* Dynamixel Interfaces configuration */
//dxl_interface_t dxl1;
//dxl_interface_t dxl2;

/* Digital servo channels configuration structures */
const uint8_t dsv_nb_channels = 2;
dsv_channel_t dsv_chan1;
dsv_channel_t dsv_chan2;


/* Definition */
#define MAX_DSV_IN_QUEUE	5

/* Local structures */
// TODO: UNUSED
typedef struct {
	uint8_t id;
	uint16_t current_Position;
	uint16_t min_Position;
	uint16_t max_Position;
}DSV_ControlTypeDef;

/* Local Variable Mutex */
static xQueueHandle xDSVMsgQueue;
//static DSV_ControlTypeDef servo1, servo2; // TODO : define a comprehensive name


// Servos
static dxl_servo_t servo1;

/* Local, Private functions */
static void OS_DSVTask(void *pvParameters);
void DSV_Create(DSV_ControlTypeDef* DSV, uint8_t id, uint16_t min_Position, uint16_t max_Position);

/**
********************************************************************************
**
**  Initialization & Configuration
**
********************************************************************************
*/

/**
  * @brief  Initialize the DSV hardware module
  */
void dsv_init(void)
{
    /* Initialize the dynamixel interfaces */
    dxl_init_itf(&dsv_chan1.dxl, BB_DSV_CHANNEL1);
    dxl_init_itf(&dsv_chan2.dxl, BB_DSV_CHANNEL2);

    /*
     * Configure the Digital Servo UART for channel 1 structure:
     *   8 bits length + 1 stop bit, no parity
     */
    dsv_chan1.uart.USART_Mode                = USART_Mode_Rx | USART_Mode_Tx;
    dsv_chan1.uart.USART_BaudRate            = 57600;
    dsv_chan1.uart.USART_HardwareFlowControl = USART_HardwareFlowControl_None;
    dsv_chan1.uart.USART_Parity              = USART_Parity_No;
    dsv_chan1.uart.USART_StopBits            = USART_StopBits_1;
    dsv_chan1.uart.USART_WordLength          = USART_WordLength_8b;

    /*
     * Configure the Digital Servo UART for channel 2 structure:
     *   8 bits length + 1 stop bit, no parity
     */
    dsv_chan2.uart.USART_Mode                = USART_Mode_Rx | USART_Mode_Tx;
    dsv_chan2.uart.USART_BaudRate            = 57600; // actual = 57143
    dsv_chan2.uart.USART_HardwareFlowControl = USART_HardwareFlowControl_None;
    dsv_chan2.uart.USART_Parity              = USART_Parity_No;
    dsv_chan2.uart.USART_StopBits            = USART_StopBits_1;
    dsv_chan2.uart.USART_WordLength          = USART_WordLength_8b;

    /* Initialize DSV Hardware */
    bb_dsv_init(dsv_chan1.dxl.itf_idx, &dsv_chan1.uart);
    bb_dsv_init(dsv_chan2.dxl.itf_idx, &dsv_chan2.uart);

    /* Configure XL-320 interface */
    dsv_chan1.dxl.protocol = DXL_V2;
    dsv_chan1.dxl.hw_send_byte = dsv_put;
    dsv_chan1.dxl.hw_receive_byte = dsv_get;
    dsv_chan1.dxl.hw_flush = dsv_flush;

    /* Configure RX-28 interface */
    dsv_chan2.dxl.protocol = DXL_V1;
    dsv_chan2.dxl.hw_send_byte = dsv_put;
    dsv_chan2.dxl.hw_receive_byte = dsv_get;
    dsv_chan2.dxl.hw_flush = dsv_flush;

    /* Create Serial Queues for channel 1 */
    dsv_chan1.rx_queue = xQueueCreate(DSV_RX_QUEUE_SIZE, sizeof(char));
    dsv_chan1.tx_queue = xQueueCreate(DSV_TX_QUEUE_SIZE, sizeof(char));

    /* Create Serial Queues for channel 2 */
    dsv_chan2.rx_queue = xQueueCreate(DSV_RX_QUEUE_SIZE, sizeof(char));
    dsv_chan2.tx_queue = xQueueCreate(DSV_TX_QUEUE_SIZE, sizeof(char));

    /* Enable hardware */
    bb_dsv_enable(dsv_chan1.dxl.itf_idx, OS_ISR_PRIORITY_DSV);
    bb_dsv_enable(dsv_chan2.dxl.itf_idx, OS_ISR_PRIORITY_DSV);

    // TEMP
     /* Initialize XL-320 Library */
     xl_320_init(XL_320_TX_ONLY);
     xl_320_set_hw_send(dsv_put);
     //xl_320_set_hw_switch(dsv_switch);

    // Initialize test servos
    dxl_init_servo(&servo1, &dsv_chan2.dxl, "RX-28");

}

/**
  * @brief  Update the hardware config and restart the
  *         DSV module
  */
void dsv_update_config(void)
{
    /* Disable hardware */
    /*bb_dsv_disable(dsv_chan1.dxl.itf_idx);
    bb_dsv_disable(dsv_chan2.dxl.itf_idx);*/

    /* Cleanup queues */
    /*vQueueDelete(dsv_chan1.rx_queue);
    vQueueDelete(dsv_chan1.tx_queue);
    vQueueDelete(dsv_chan2.rx_queue);
    vQueueDelete(dsv_chan2.tx_queue)
*/
    // Restart the entire initialization
    bb_dsv_init(dsv_chan1.dxl.itf_idx, &dsv_chan1.uart);
    bb_dsv_init(dsv_chan2.dxl.itf_idx, &dsv_chan2.uart);
}

/**
********************************************************************************
**
**  Low-level routines
**
********************************************************************************
*/

/**
  * @brief  Add a byte to send through dsv channel
  *         Might be started right away or stored in the TX Queue.
  * @param  chan_idx: DSV channel
  * @param  tx_data: data to send
  * @retval pdPASS if the character was sent or added to the TX Queue
  *         pdFAIL if the TX Queue is full
  */
uint8_t dsv_put(uint8_t chan_idx, uint8_t tx_data)
{
    QueueHandle_t* tx_queue;
    USART_TypeDef* usart_if;

    if(chan_idx == BB_DSV_CHANNEL1) {
        tx_queue = &dsv_chan1.tx_queue;
        usart_if = DSV_COM;

    } else if(chan_idx == BB_DSV_CHANNEL2) {
        tx_queue = &dsv_chan2.tx_queue;
        usart_if = RS485_COM;
    }

    /* If the queue is empty and no message is being transmitted,
     * the line is idle so we can initiate directly the transmission.
     */
    if((uxQueueMessagesWaiting(*tx_queue) == 0) &&
       (USART_GetFlagStatus(usart_if, USART_FLAG_TXE) == SET)) {

        bb_dsv_switch(chan_idx, DXL_MODE_TX);
        USART_ITConfig(usart_if, USART_IT_TC, ENABLE);
        USART_SendData(usart_if, (uint16_t) tx_data);

        return pdPASS;

    /* Otherwise, at least 1 transmission is pending,
     * so we add it the the transmit queue.
     */
    } else {

        if(xQueueSend(*tx_queue, &tx_data, DSV_TX_TIMEOUT) == pdPASS)
        {
            USART_ITConfig(usart_if, USART_IT_TC, ENABLE);
            return pdPASS;
        } else {
            return pdFAIL;
        }
    }

}
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

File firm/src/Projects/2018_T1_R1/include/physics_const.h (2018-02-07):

/* -----------------------------------------------------------------------------
 * BlueBoard
 * I-Grebot 2018
 * -----------------------------------------------------------------------------
 * @file       physics_const.h
 * @author     Pierrick
 * @date       Jan 27, 2018
 * @version    V1.0
 * -----------------------------------------------------------------------------
 * @brief
 *   This file defines all physical constants like distances, positions, speed
 *   accelerations are time. It concerns the robot(s) as well as the opponent(s)
 *   and playground.
 * -----------------------------------------------------------------------------
 * Versionning informations
 * Repository: http://svn2.assembla.com/svn/paranoid_android/
 * -----------------------------------------------------------------------------
 * $Rev:: 1464                                                                 $
 * $LastChangedBy:: Pierrick_Boissard                                          $
 * $LastChangedDate:: 2016-05-02 15:38:42 +0200 (lun., 02 mai 2016)            $
 * -----------------------------------------------------------------------------
 */

#ifndef PHYSICS_CONST_H_
#define PHYSICS_CONST_H_

#include <stdint.h>

/**
********************************************************************************
**
**  Mechanical constants of our robot
**
********************************************************************************
*/

/* Distance between motorized wheels, in millimeters */
#define PHYS_ROBOT_MOTORS_TRACK_MM          ((double)  162.5)

/* Distance between quadrature encoder wheels, in millimeters */
#define PHYS_ROBOT_ENCODERS_TRACK_MM        ((double)  270.8)

/* Nominal Diameter of a quadrature encoder wheel, in millimeters */
#define PHYS_ROBOT_ENCODER_WHEEL_DIAM_MM    ((double)   57.2) // R: 57.2 / L: 57.5

/* Number of impulsions of the quadrature encoder per revolution */
#define PHYS_ROBOT_ENCODER_NB_IMP_PER_REV   ((double) 4096.0)

/* Encoder wheel gains to compensate for forward/backward rotation
 * (adjust sign) and diameter variations */
#define PHYS_ROBOT_ENCODER_LEFT_GAIN        ((double)  1.0000)
#define PHYS_ROBOT_ENCODER_RIGHT_GAIN       ((double) -1.0050)

/* Centrifugal compensation coefficient. Value TO BE ADJUSTED */
#define PHYS_ROBOT_CENTRIFUGAL_COEF         ((double)   5.0)

/* Quadrature encoders conversion ratio between a number
 * of impulsions and a distance (in mm). Simply divide by the
 * number of impulsions per revolution by the perimeter of a quadrature
 * encoder wheel (nominal value) */
#define PHYS_ROBOT_NB_IMP_PER_MM      (PHYS_ROBOT_ENCODER_NB_IMP_PER_REV \
                                    / (M_PI * PHYS_ROBOT_ENCODER_WHEEL_DIAM_MM))

/**
********************************************************************************
**
**  Motion control filters constants
**
********************************************************************************
*/

/* Control System in Distance filters parameters */
#define PHYS_CS_D_PID_KP                    ((int16_t)   10000)
#define PHYS_CS_D_PID_KI                    ((int16_t)      0)
#define PHYS_CS_D_PID_KD                    ((int16_t)   1000)
#define PHYS_CS_D_PID_MAX_IN                ((int32_t)      0)
#define PHYS_CS_D_PID_MAX_I                 ((int32_t)   5000)
#define PHYS_CS_D_PID_MAX_OUT               ((int32_t)      0)
#define PHYS_CS_D_PID_OUT_SHIFT             ((uint8_t)     12)
#define PHYS_CS_D_PID_DRV_FILTER            ((uint8_t)      4)
#define PHYS_CS_D_QUAD_POS_SPEED            ((uint32_t)  1200)
#define PHYS_CS_D_QUAD_NEG_SPEED            ((uint32_t)  1200)
#define PHYS_CS_D_QUAD_POS_ACCEL            ((uint32_t)    40)
#define PHYS_CS_D_QUAD_NEG_ACCEL            ((uint32_t)    40)

/* Control System in Angle filters parameters */
#define PHYS_CS_A_PID_KP                    ((int16_t)   2500)
#define PHYS_CS_A_PID_KI                    ((int16_t)      0)
#define PHYS_CS_A_PID_KD                    ((int16_t)   1000)
#define PHYS_CS_A_PID_MAX_IN                ((int32_t)      0)
#define PHYS_CS_A_PID_MAX_I                 ((int32_t)   5000)
#define PHYS_CS_A_PID_MAX_OUT               ((int32_t)      0)
#define PHYS_CS_A_PID_OUT_SHIFT             ((uint8_t)     11)
#define PHYS_CS_A_PID_DRV_FILTER            ((uint8_t)      4)
#define PHYS_CS_A_QUAD_POS_SPEED            ((uint32_t)  1200)
#define PHYS_CS_A_QUAD_NEG_SPEED            ((uint32_t)  1200)
#define PHYS_CS_A_QUAD_POS_ACCEL            ((uint32_t)    24)
#define PHYS_CS_A_QUAD_NEG_ACCEL            ((uint32_t)    24)

/* Trajectory Manager parameters */
#define PHYS_TRAJ_D_DEFAULT_SPEED           ((int16_t)    1500)
#define PHYS_TRAJ_A_DEFAULT_SPEED           ((int16_t)    800)
#define PHYS_TRAJ_DEFAULT_WIN_D             ((double)    30.0)
#define PHYS_TRAJ_DEFAULT_WIN_A_DEG         ((double)     5.0)
#define PHYS_TRAJ_DEFAULT_WIN_A_START_DEG   ((double)    30.0)
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

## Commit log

2016-12-04 Fixed incorrect UART definition for 9b word-length mode. Added bootloader batch script.
    [main.c]
2017-01-01 Shell fully functionnal
    Debug (Serial) Interface fully managed with interrupts & Queues.
    Still some work todo with the CLI and the PROBE function
2017-01-08 Added shell probe function
2017-01-21 Merged firm_blueboard and elec_blueboard into 1 repository
    [BlueBoard_v1.brd, BlueBoard_v1.csv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]
2017-02-11 Basic shell Digital Servo Command function
2017-04-09 Finally fixed the f* problem with printf float
    [BlueBoard v1.ioc, main.c, shell_commands.c]
2017-04-18 Fixed errors in the dsv shell command and dxl registers module
    [digital_servo.c, shell_commands.c]
2017-04-23 Basic bare-bone strategy + AI + task system -- missing high level mgmt
    [digital_servo.c]
2017-04-29 Added beacons SPI doc
    [beacons_spi.xlsx]
2017-05-03 BOM with 2017 re-order
    [BlueBoard_v1_bom.xlsx]
2017-05-06 Physics update, temporary printing func for tests
2017-05-19 Basic working SPI hardware for beacons
2017-05-21 Fixed stack overflow of AI task when receiving notification
    [avoidance.h]
2017-05-22 Fixed some important AVD errors, updated ai, tasks and feedbacks to GUI
    [avoidance.h]
2018-02-07 go to home automation switch
    creation of the ai task
    shut the avoidance
    [physics_const.h, strategy.h]

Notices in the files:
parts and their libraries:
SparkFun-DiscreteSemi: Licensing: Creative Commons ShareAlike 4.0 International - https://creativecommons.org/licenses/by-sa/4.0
